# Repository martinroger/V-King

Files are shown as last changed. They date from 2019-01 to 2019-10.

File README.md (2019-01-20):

The target is to create a cheap 500mmx500mmx500mm version !

Original Readme by Roy :

# V-King Pro 3d Printer
The non rod CoreXY V-Slot 3d Printer by Roy Berntsen

In this repository you will find the print files, source files and documentation for the V-King 3D printer. If you are missing a part or information of feel free to file an issue on github

I would appreciate if you buy me a coffe to keep the pace going in this project:

<a href="https://www.buymeacoffee.com/pro3d" target="_blank">Buy Me A Coffee</a>

You can be a supporter of the develompent on patreon here: https://www.patreon.com/pro3d

Community links: https://www.facebook.com/vking3d/ - https://www.facebook.com/groups/viking3d/

Here is a video covering the basics and benefits of this design: https://youtu.be/wINF7qM0DQU

All files are released according to the following license unless specified differently in the file or directory:
CC-by-NC: http://creativecommons.org/licenses/by-nc/3.0/

Roy Berntsen - Research and Development

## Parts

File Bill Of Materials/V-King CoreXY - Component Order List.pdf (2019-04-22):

V-King - Components to Buy

ALL HARDWARE KIT HERE ->> | MakerSupplies V-King Mechanical Kit (http://makersupplies.dk/72-v-king-corexy-3d-printer)
Click link to product supplier | Research, Development & Design by: | Roy Berntsen
Part Name | Description | BOM Quantity Unit Price | | Bulk Price
Frame Parts | Complete Kit (http://makersupplies.dk/72-v-king-corexy-3d-printer)
2020 V-Slot 500 (http://[s0l0];/#/56-color-silver_grey_anodized/40-length-500mm) | OpenBuild V-Slot 500mm | 16 | EUR 5,0 | EUR 80,0
2020 V-Slot 480 (http://[s0l1];/#/56-color-silver_grey_anodized/40-length-500mm) | OpenBuild V-Slot 480mm (http://makersupplies.dk/linear-rail/188-linear-rail-custom-cut-v-slot-rail-per-cut.html) | 1 | EUR 6,0 | EUR 6,0
3 Way V-Slot Corner (http://makersupplies.dk/brackets/32-brackets-cube-corner-connector.html?search_query=3+way&results=18) | 3 Way Corner Bracket | 8 | EUR 4,0 | EUR 32,0
2028 Corner Bracket (http://s.click.aliexpress.com/e/BqJqfQF) | Frame Corner Joint Brackets | 20 | | 7,00
Wheels
Solid V-Wheel Kit (http://makersupplies.dk/wheels/67-wheels-solid-v-wheel-kit.html) | OpenBuild V-Slot Big Wheels | 21 | EUR 5,0 EUR 105,0
Estimated Frame Kit Price | | | | EUR 230,0
Component Part Name | BOM Quantity Bulk Quantity | Bulk Price
Build Plate 1400 cm^2 (http://clever3d.de/epages/7a4290fc-7c7f-46cc-9b99-eadef22228e2.sf/en_US/) | 360x410x8mm Aluminum | 1 | 1 | 90,00
Controller - MKS Gen L V1.0 (http://s.click.aliexpress.com/e/uB2fyVN) | Ramps Controller | 1 | 1 | 20,00
Controller LCD 12864 (http://s.click.aliexpress.com/e/bRJkG02c) | LCD Controller Panel | 1 | 1 | 12,00
Drivers - A4988 (http://s.click.aliexpress.com/e/cln5G0dw) | ZE Stepper Drivers | 2 | 4 | 10,00
Drivers - TMC2208 (http://s.click.aliexpress.com/e/bPs1Gu4g) | XY Stepper Drivers | 2 | 4 | 25,00
End Stop - Optical Sensor (http://s.click.aliexpress.com/e/Im2VNR3) | Optical Endstop Sensor | 2 | 6 | 3,00
Extruder (http://s.click.aliexpress.com/e/bH9je2h6) | Titan Original Here (https://e3d-online.com/titan-extruder) | 1 | 1 | 20,00
Fan - Layer Fan 12/24V (http://s.click.aliexpress.com/e/EDFqKMu) | Fan for filament cooling | 1 | 1 | 5,00
GT2 Idler Pulley 20T (http://s.click.aliexpress.com/e/bNQNlORm) | Thoothed Idler Pulley | 8 | 10 | 10,00
GT2 Idler Pulley Smooth (http://s.click.aliexpress.com/e/bNQNlORm) | Smooth Pulley | 10 | 10 | 10,00
GT2 Motor Pulley 20T (http://s.click.aliexpress.com/e/b71XZzSu) | Thoothed Motor Pulley | 4 | 4 | 5,00
GT2 Timing Belt (http://s.click.aliexpress.com/e/E6yV3BM) | Reinforced Timing Belt | 7 | 10 | 10,00
Hotend - J-Head/E3d Clone (https://www.aliexpress.com/store/product/3D-printer-parts-e3d-V6-24V-remote-Bowen-print-J-head-Hotend-extruder-1meter-Teflon-tube/1494743_32869495725.html) | e3d V6 Original Here (https://e3d-online.com/v6) | 1 | 1 | 5,00
Power Supply 24V (http://s.click.aliexpress.com/e/bUwbSgN2) | 240W 24V PSU | 1 | 1 | 20,00
Power Switch - Fused (http://s.click.aliexpress.com/e/b2QUtcoC) | AC Inlet to PSU with Fuse | 1 | 1 | 7,00
Probe - 3D Touch (http://s.click.aliexpress.com/e/bhxMAOUo) | Original Probe here (https://www.antclabs.com/) | 1 | 1 | 15,00
Silicone Heatpad 350*400 (http://s.click.aliexpress.com/e/bWGHdGPI) | Ask for 110 AC if needed | 1 | 1 | 30,00
Solid State Relay (http://s.click.aliexpress.com/e/iQVbe2z) | SSR 40A | 1 | 1 | 4,00
Stepper Motor 1.7A Nema 17 (http://s.click.aliexpress.com/e/dZN2aDi) | Nema 17 Stepper motor | 4 | 4 | 30,00
Worm Gear (https://rover.ebay.com/rover/1/711-53200-19255-0/1?icep_id=114&ipn=icep&toolid=20004&campid=5338443015) | 1:20 Worm Gear Set | 1 | 1 | 10,00
Worm Gear Bearings (http://s.click.aliexpress.com/e/c5afxP5q) | 5id-16od-5w Ball bearings | 4 | 10 | 4,00
Worm Gear Rod (https://rover.ebay.com/rover/1/711-53200-19255-0/1?icep_id=114&ipn=icep&toolid=20004&campid=5338443015) | 5mm X 555 mm Steel rod | 1 | 1 | 20,00
Estimated Component Retail Price | No fasteners or cables included | EUR 365,0
Komplete Mechanichal Kit | Fasteners included | | | Bulk Price
MakerSupplies Mechanical Kit (http://makersupplies.dk/72-v-king-corexy-3d-printer) | | | | EUR 315,00

If you like to support - Buy me a coffe here: https://www.buymeacoffee.com/pro3d

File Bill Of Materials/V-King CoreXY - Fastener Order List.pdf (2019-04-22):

List of Fasteners to buy at any hardware supplier

Research, Development & Design by

## Roy Berntsen

Fasteners | Type | Order Quantity Est. Unit Price Est. Bulk Price
M3 NUT | Hex Nut - M3 | 25 | 0,1 | 2,5
M3 WASHER | Washer Simple M3 | 25 | 0,1 | 2,5
M3x10 | DIN 912 | 25 | 0,1 | 2,5
M3X25 | DIN 912 | 10 | 0,1 | 1
M3x8 | DIN 912 | 25 | 0,1 | 2,5
M4 Hex NUT | Hex Nut - M4 | 10 | 0,1 | 1
M4 Hex Nut lock | Hex Locking Nut - M4 | 10 | 0,1 | 1
M4 WASHER | Washer Simple M4 | 10 | 0,1 | 1
M4x16 | DIN 912 | 10 | 0,1 | 1
M4x20 | DIN 912 | 10 | 0,1 | 1
M5 GT2 Idler Shim | Precision Shim for GT2 idlers/pulleys | 25 | 0,1 | 2,5
M5 Hex Nut | Standard Nut M5 | 20 | 0,1 | 2
M5 Hex Nut lock | Hex Locking Nut - m5 | 40 | 0,1 | 4
M5 T-Nut Hammer (http://s.click.aliexpress.com/e/bswuOzVQ) | Drop In type Hammer Nut | 50 | 0,1 | 5
M5 T-Nut Square (http://s.click.aliexpress.com/e/bn7WcvoG) | T-Nut Sqare M5 | 100 | 0,1 | 10
M5 WASHER | Washer Simple M5 | 150 | 0,1 | 15
M5x10 | DIN 912 | 100 | 0,1 | 10
M5x14 | DIN 912 | 10 | 0,1 | 1
M5x20 Hex | Hex Head | 20 | 0,1 | 2
M5X25 | DIN 912 | 10 | 0,1 | 1
M5x30 | DIN 912 | 20 | 0,1 | 2
M5x35 | DIN 912 | 10 | 0,1 | 1
M5x35 HEX | Hex Head | 10 | 0,1 | 1
M5x8 Countersink (http://s.click.aliexpress.com/e/cBsxDBlm) | DIN 7991 | 25 | 0,1 | 2,5
Estimated fastener price in total: | 75
Cables | Type | Order Quantity Est. Unit Price Est. Bulk Price

If you like to support - Buy me a coffe here: https://www.buymeacoffee.com/pro3d

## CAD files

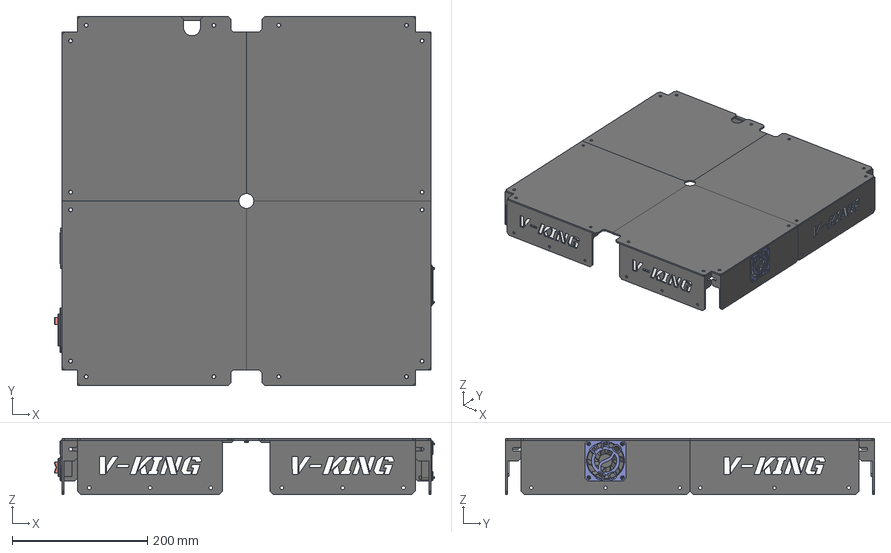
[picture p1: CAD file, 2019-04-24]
Source Files/STEP Files/Bottom Cabinet Assy v4.step
562.7 x 546.0 x 83.0 mm
V-King Led Plate x 6
Fan Grill 60 x 2
Fan House
Fan
M3 WASHER x 4
M3 NUT x 4
M3x20 x 4
Enclosure Lid AD x 2
Enclosure Lid BC
Enclosure Lid B

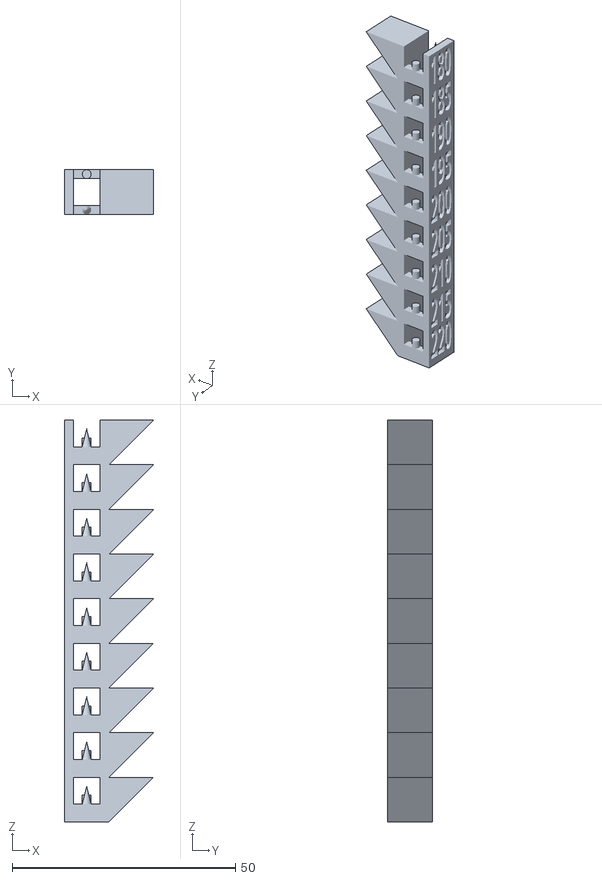
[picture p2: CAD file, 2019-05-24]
Part Print Files/Calibration Files/Temp Tower.stl
20.0 x 10.0 x 90.0

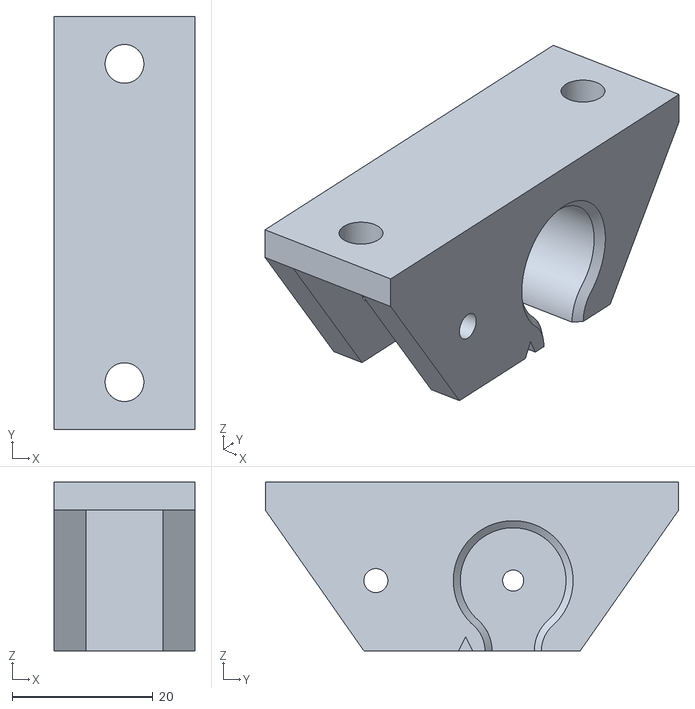
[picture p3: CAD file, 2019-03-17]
Part Print Files/Optional Files/3mm Idler Brackets/Z Idler_3mm Top Mount_R_1x.stl
20.0 x 58.7 x 24.0

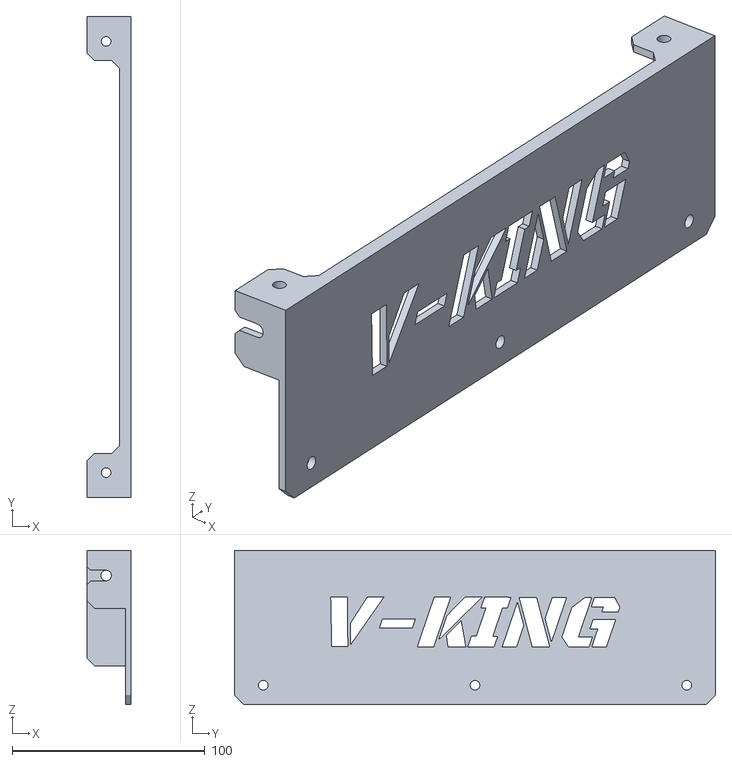
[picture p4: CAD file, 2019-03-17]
Part Print Files/Optional Files/Bottom Enclosure Files/Cover Side B2.stl
23.0 x 250.0 x 80.0

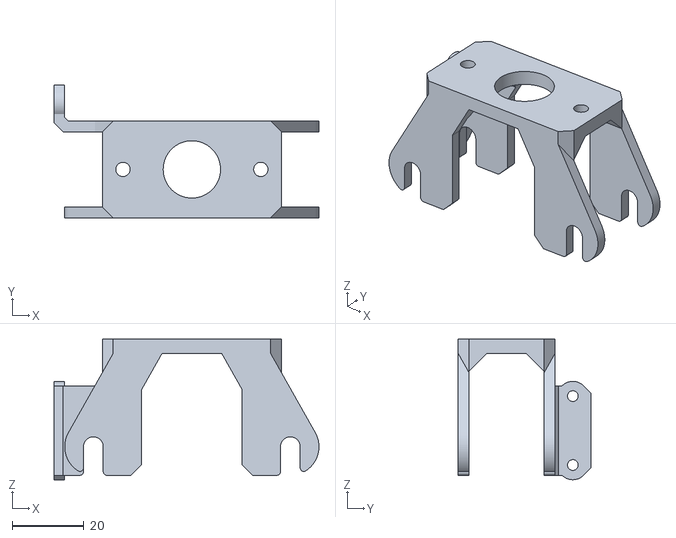
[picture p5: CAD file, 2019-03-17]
Part Print Files/Optional Files/Bowden Support/Bowden Carrier Buddy Support.stl
74.0 x 37.0 x 39.2

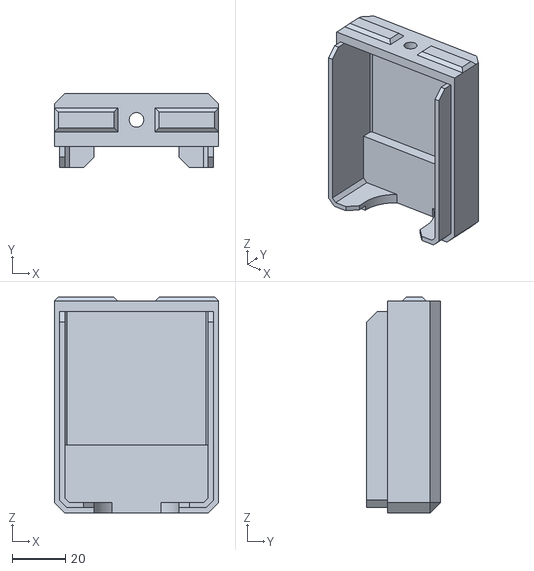
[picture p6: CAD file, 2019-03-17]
Part Print Files/Optional Files/Junction Box/Junction Base.stl
62.0 x 28.0 x 81.5

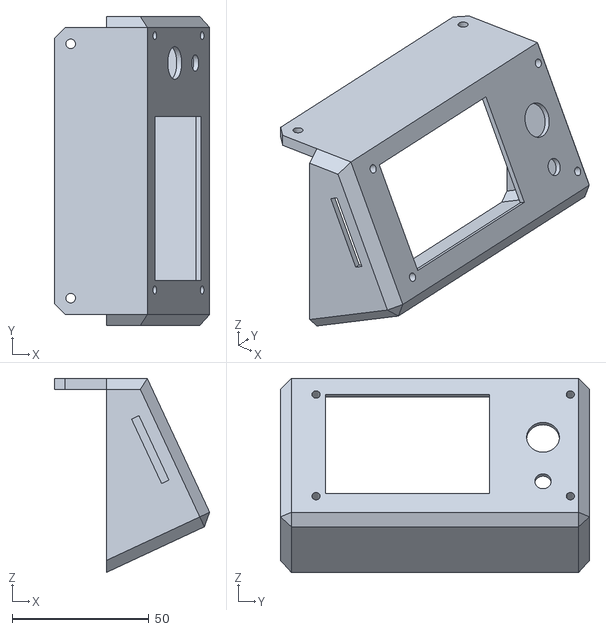
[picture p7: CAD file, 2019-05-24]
Part Print Files/Optional Files/Mini12864 LCD Cabinet.stl
56.8 x 113.0 x 71.0

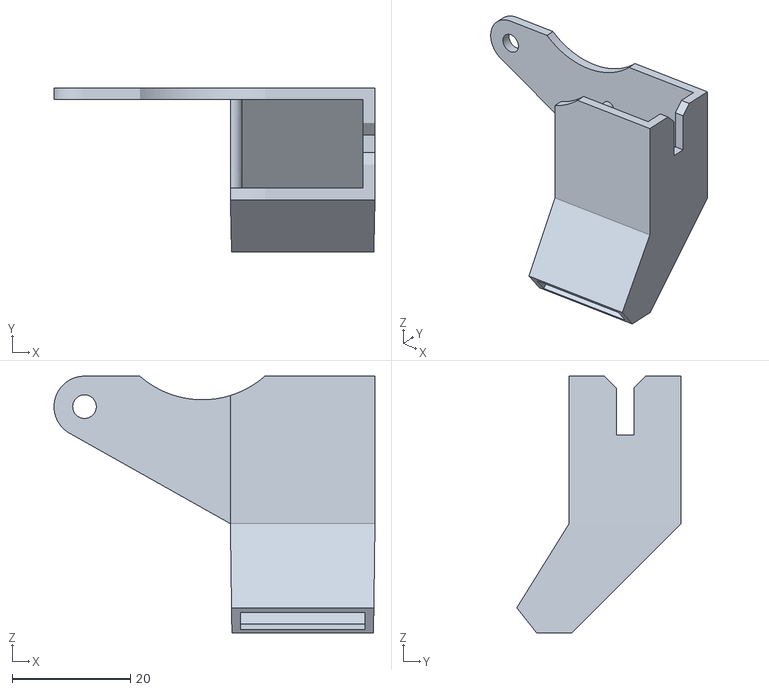
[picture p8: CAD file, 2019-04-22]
Part Print Files/Optional Files/Misc/5015 Layer Fan - Side Blower_1x.stl
54.4 x 27.9 x 43.5

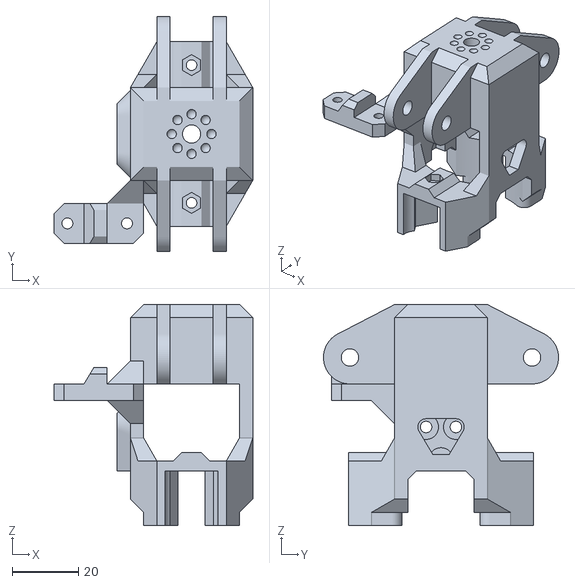
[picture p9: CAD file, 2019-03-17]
Part Print Files/Optional Files/X-Carriers/X-Carrier Chimera.stl
60.0 x 71.0 x 66.8

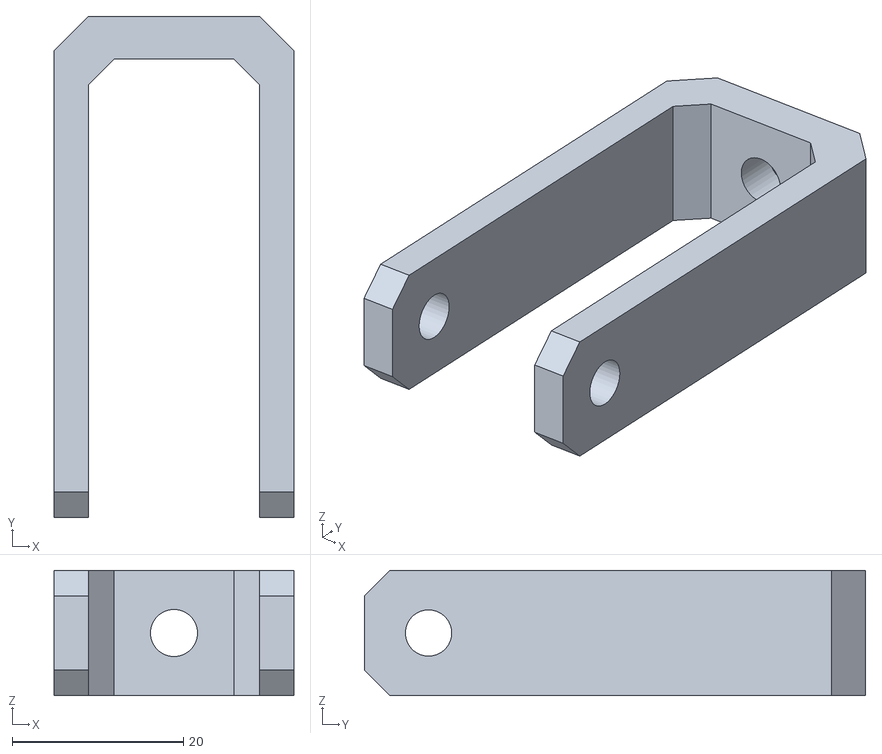
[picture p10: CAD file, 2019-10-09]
Part Print Files/Stock Part Files/Base Frame Parts/XY Belt Tensioner/XY Belt Tension Fork_2x_SN_BO.stl
28.0 x 58.5 x 14.6

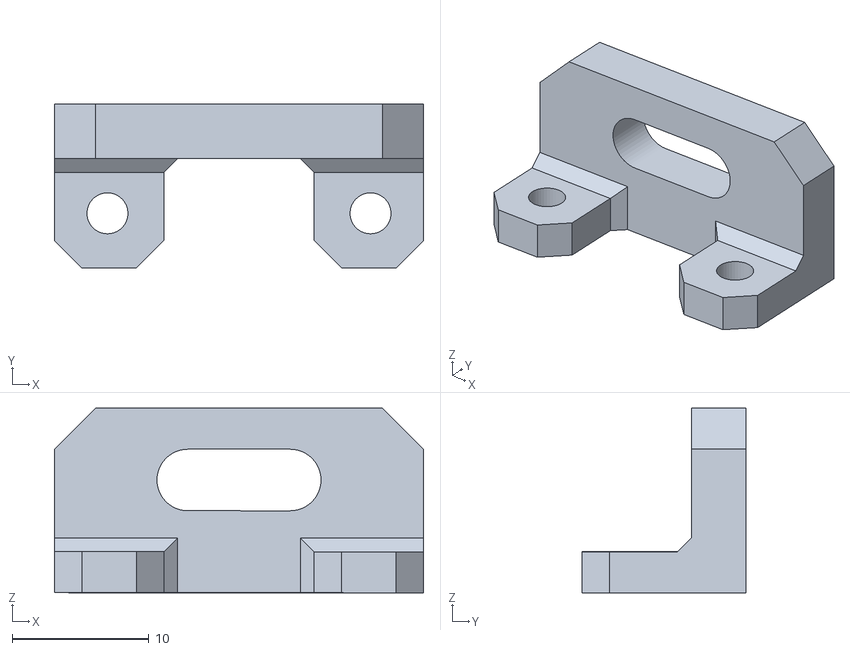
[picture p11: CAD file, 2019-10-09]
Part Print Files/Stock Part Files/Base Frame Parts/Y EndStop Bracket_1x_SN_BO.stl
27.0 x 12.0 x 13.5

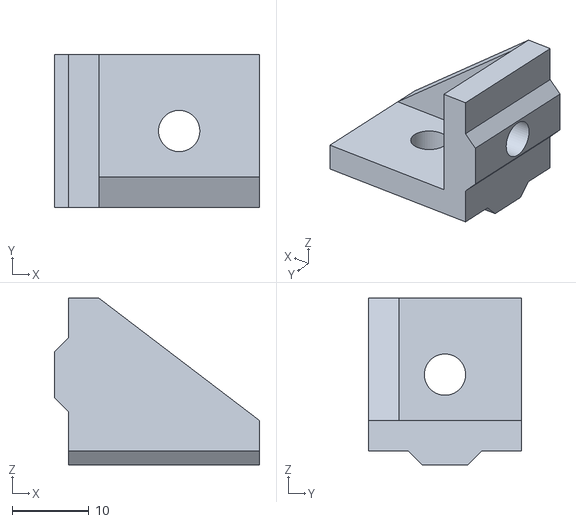
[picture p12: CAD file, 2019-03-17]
Part Print Files/Stock Part Files/Bed Supports/Bed L Bracket_4x.stl
26.8 x 20.0 x 21.8

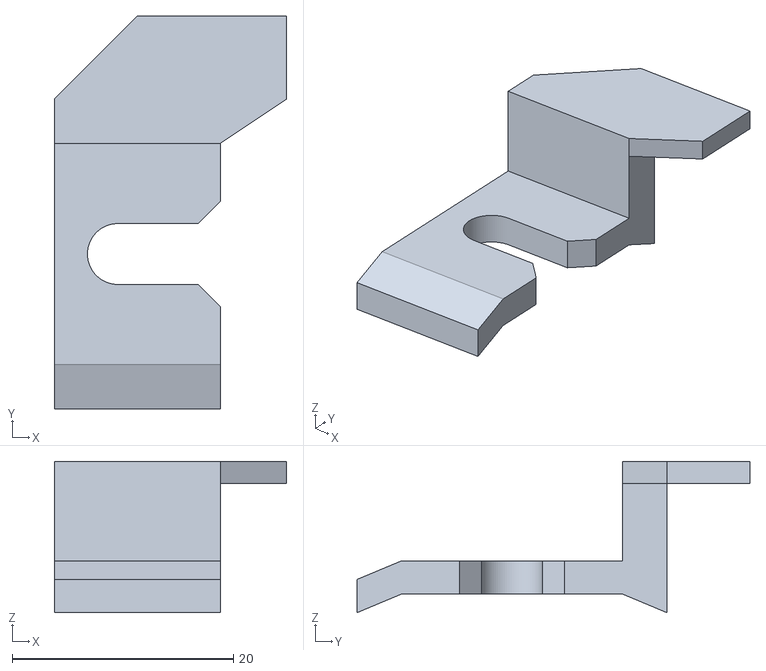
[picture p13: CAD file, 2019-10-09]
Part Print Files/Stock Part Files/X Axis Parts/X Carrier Parts/X EndStop Flag_1x.stl
21.0 x 35.5 x 13.7

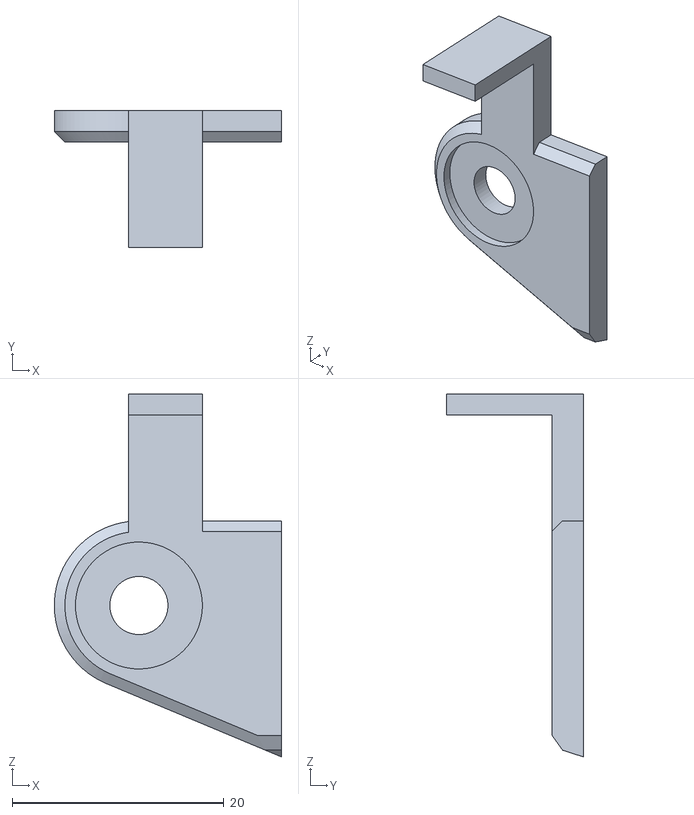
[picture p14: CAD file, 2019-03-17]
Part Print Files/Stock Part Files/X Axis Parts/Y EndStop Flag_1x.stl
21.5 x 13.0 x 34.3

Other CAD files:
Part Print Files/Stock Part Files/Z Drive Parts/Z Belt Anchor Lid R_1x.stl
Part Print Files/Tools/Bed Frame Hooks.stl
Part Print Files/Tools/Test Jig Files/e3d Fan Buddy.stl
Source Files/STEP Files/bullshit.step
Part Print Files/Calibration Files/Stringing_Test.stl
Part Print Files/Optional Files/3mm Idler Brackets/XY Idler_3mm Corner_2x.stl
Part Print Files/Optional Files/3mm Idler Brackets/Z Idler_3mm Bed Bracket_2x.stl
Part Print Files/Optional Files/3mm Idler Brackets/Z Idler_3mm Bed Support_2x.stl
Part Print Files/Optional Files/3mm Idler Brackets/Z Idler_3mm Top Mount_M_1x.stl
Part Print Files/Optional Files/Bottom Enclosure Files/2020 Cable Sleeve Buddy.stl
Part Print Files/Optional Files/Bottom Enclosure Files/Center Lid Nut.stl
Part Print Files/Optional Files/Bottom Enclosure Files/Center Lid Support.stl
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

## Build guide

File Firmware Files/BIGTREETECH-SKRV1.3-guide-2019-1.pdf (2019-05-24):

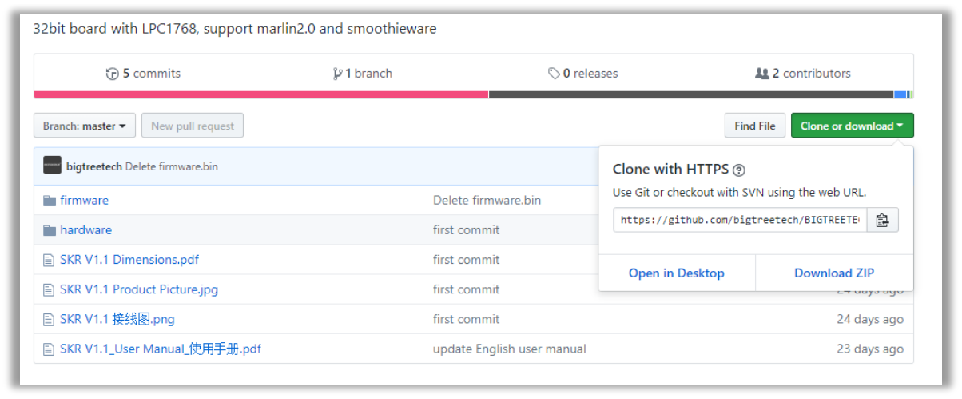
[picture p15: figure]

BIGTREETECH SKR V1.3 guide 2019 – V1 by Jupa Creations Page 1

BIGTREETECH/BIQU SKR V1.3 instruction guide by Jupa Creations

All official information like schematics and hardware about this 32 bits 3D printer mainboard can be found on the BIGTREETECH official GITHUB site. (https://github.com/bigtreetech/BIGTREETECH-SKR-V1.3)

This instruction guide is to show you how to install Marlin 2.0 firmware to the SKR V1.3 board in general. It does not take in account machine and other hardware specific settings!

You can use VSCode or Atom.IO + Platform IO to compile Marlin2.0 to BIGTREETECH/BIQU SKR V1.3

Intended for use with a REPRAP_DISCOUNT_FULL_GRAPHIC_SMART_CONTROLLER 128x64 LCD display by standard with two 10 wire ribbon cables.

Download the Marlin2.0 firmware from Marlin 2.0 github firmware version (https://github.com/MarlinFirmware/Marlin/tree/bugfix-2.0.x) and click.

Click “Download ZIP”

Remark if you use Octoprint, do not use the BIGTREETECH firmware version itself but download Marlin 2.0 github firmware version (https://github.com/MarlinFirmware/Marlin/tree/bugfix-2.0.x) and modify it to your needs.

When the download is complete, unzip the file to a known place.

N this example we use VScode

Download the VScode from https://code.visualstudio.com/Download. Choose the version which is compliant with your PC operating system.

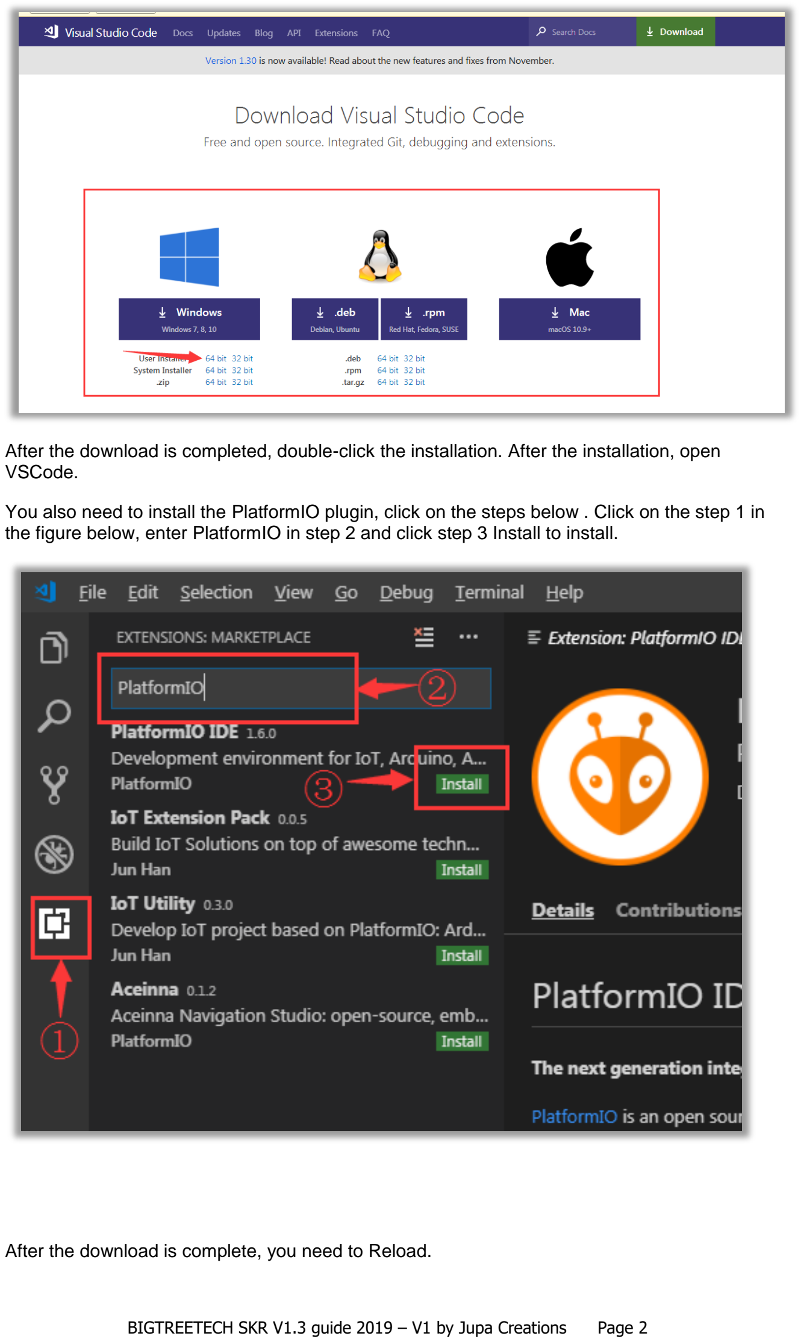
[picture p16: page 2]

BIGTREETECH SKR V1.3 guide 2019 – V1 by Jupa Creations Page 2

After the download is completed, double-click the installation. After the installation, open VSCode.

You also need to install the PlatformIO plugin, click on the steps below . Click on the step 1 in the figure below, enter PlatformIO in step 2 and click step 3 Install to install.

After the download is complete, you need to Reload.

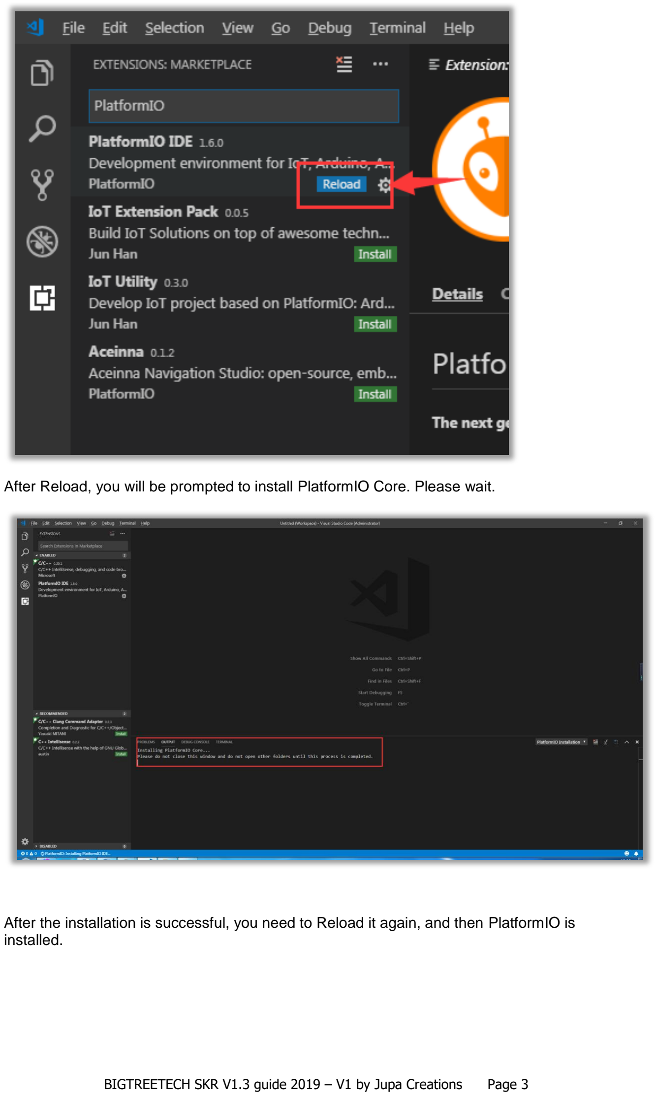
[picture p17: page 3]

BIGTREETECH SKR V1.3 guide 2019 – V1 by Jupa Creations Page 3

After Reload, you will be prompted to install PlatformIO Core. Please wait.

After the installation is successful, you need to Reload it again, and then PlatformIO is installed.

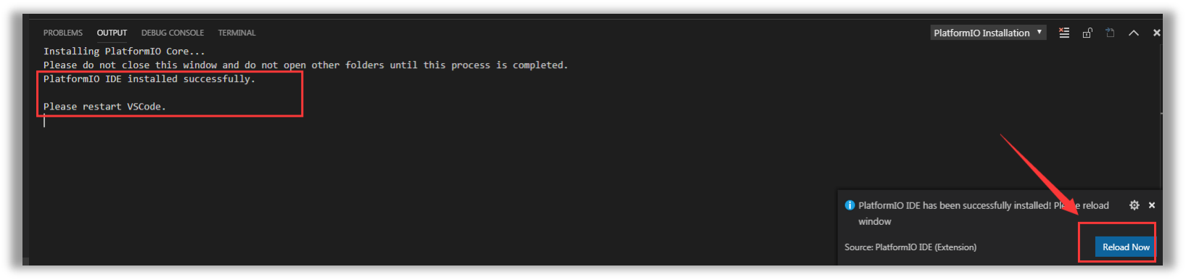
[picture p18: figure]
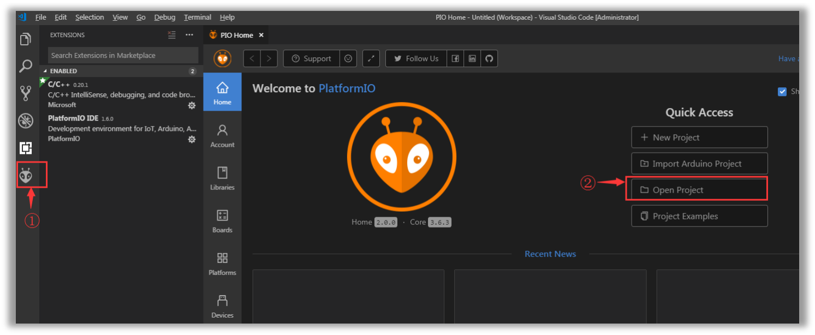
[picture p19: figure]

BIGTREETECH SKR V1.3 guide 2019 – V1 by Jupa Creations Page 4

In the lower left corner of VSCode, you can see the icon (1), which is PlatformIO plug-in. Click
(2) Open Project to Open the Project.

Find the marlin2.0 source directory where you extracted in the very first step, and click Open.

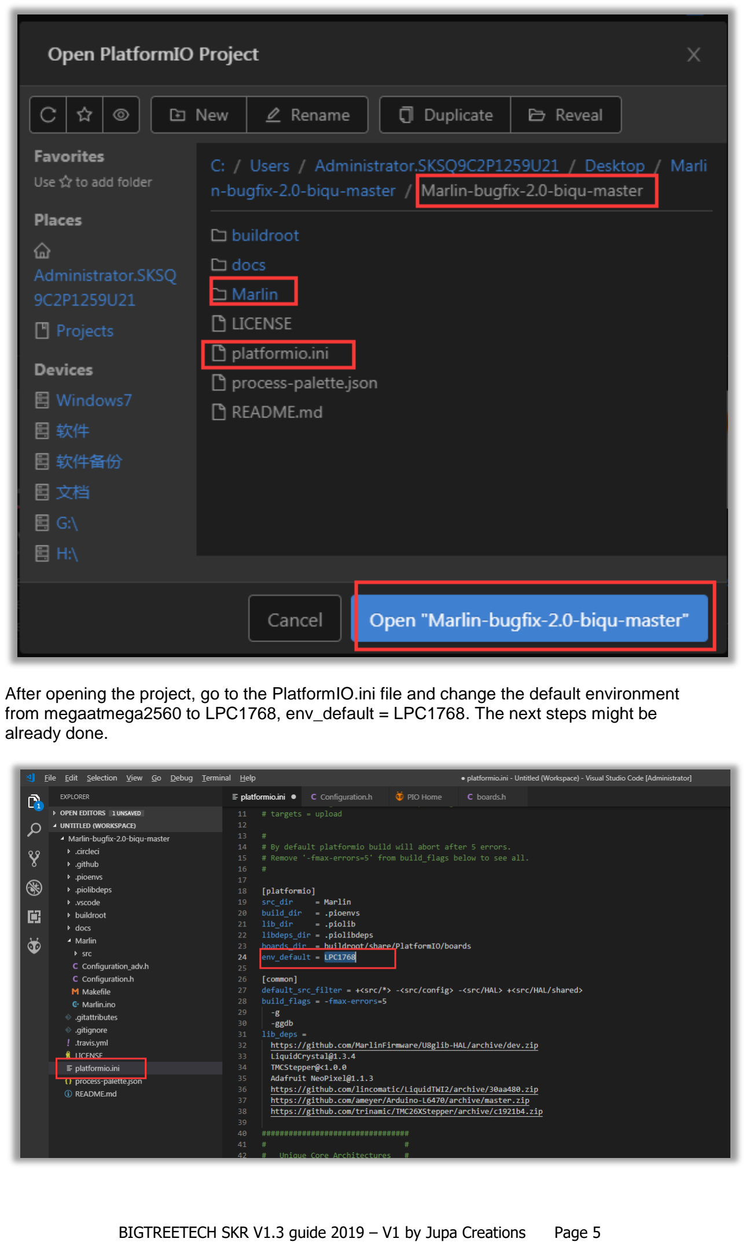
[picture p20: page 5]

BIGTREETECH SKR V1.3 guide 2019 – V1 by Jupa Creations Page 5

After opening the project, go to the PlatformIO.ini file and change the default environment from megaatmega2560 to LPC1768, env_default = LPC1768. The next steps might be already done.

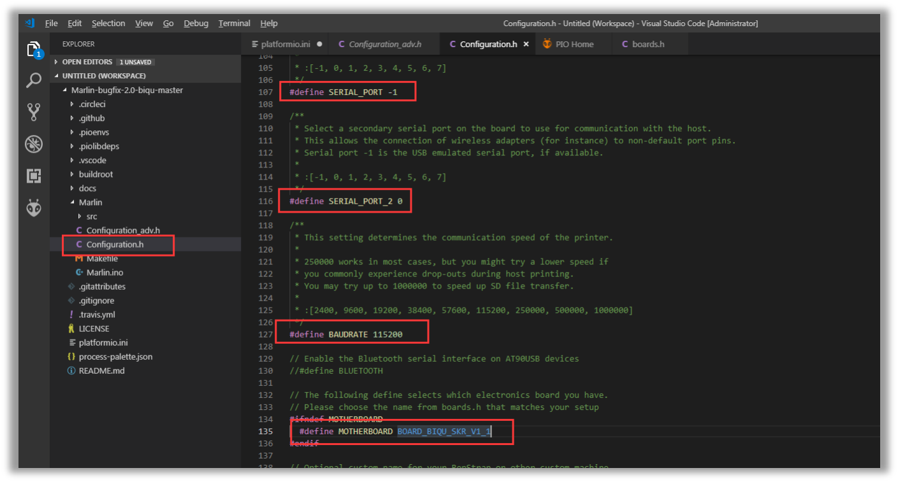
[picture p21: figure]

BIGTREETECH SKR V1.3 guide 2019 – V1 by Jupa Creations Page 6

Then go to the configuration.h file and if not yet done modify it to

#define SERIAL_PORT 0

#define SERIAL_PORT_2 -1

#define BAUDRATE 115200

#define MOTHERBOARD BOARD_BIQU_SKR_V1_3

If you like to use a BL-touch you have to change some code.

In the same Configuration.h

Modify the following lines:

//#define BLTOUCH and change to
#define BLTOUCH

//#define AUTO_BED_LEVELING_BILINEAR and change to #define AUTO_BED_LEVELING_BILINEAR

// #define Z_SAFE_HOMING and change to
#define Z_SAFE_HOMING

// #define ENCODER_PULSES_PER_STEP 4 and change to #define ENCODER_PULSES_PER_STEP 4

// #define REVERSE_ENCODER_DIRECTION and change to
#define REVERSE_ENCODER_DIRECTION

//#define REPRAP_DISCOUNT_FULL_GRAPHIC_SMART_CONTROLLER and change to #define REPRAP_DISCOUNT_FULL_GRAPHIC_SMART_CONTROLLER

If you like to activate Babystepping switch to Configuration_adv.h

//#define BABYSTEPPING and change to
#define BABYSTEPPING

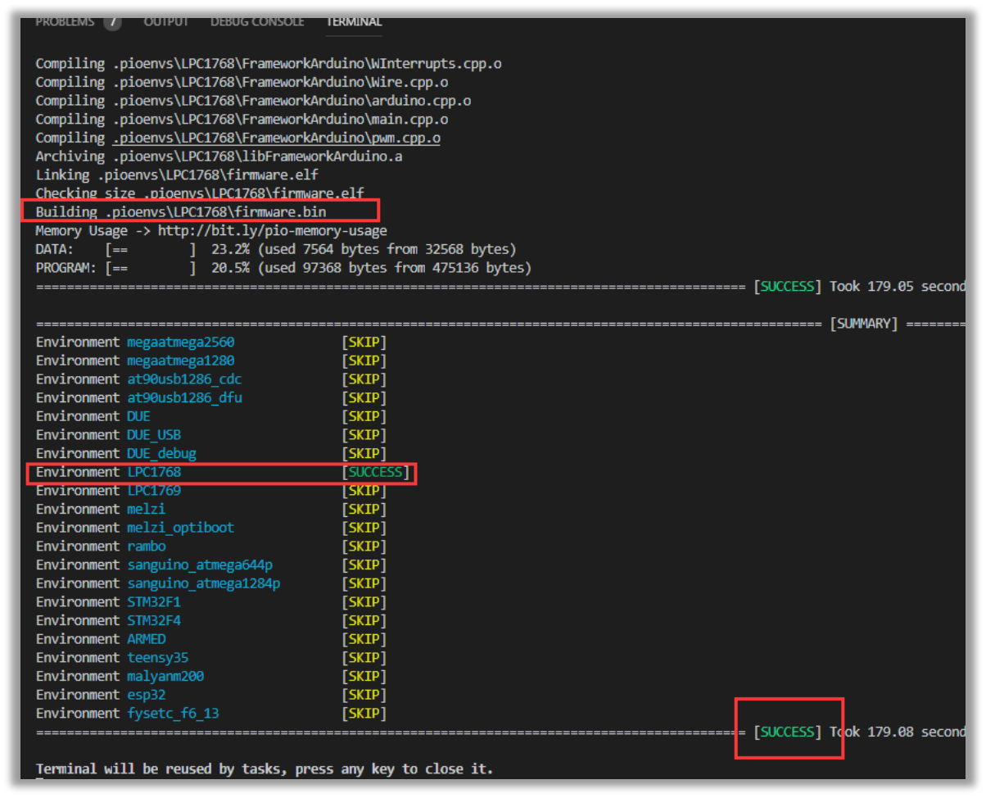
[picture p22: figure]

BIGTREETECH SKR V1.3 guide 2019 – V1 by Jupa Creations Page 7

//#define DOUBLECLICK_FOR_Z_BABYSTEPPING and change to #define DOUBLECLICK_FOR_Z_BABYSTEPPING

//#define BABYSTEP_ZPROBE_OFFSET and change to #define BABYSTEP_ZPROBE_OFFSET

//#define BABYSTEP_ZPROBE_GFX_OVERLAY and change to #define BABYSTEP_ZPROBE_GFX_OVERLAY

#define BABYSTEP_MULTIPLICATOR 1 and change to

#define BABYSTEP_MULTIPLICATOR 20

If your original BL-touch, clone TL-touch or clone BT-touch is dropping the pin during printing switch to Marlin/scr/inc/conditionals_LCD.h and change the following code:

#define BLTOUCH_STOW 100 // was 90

#define BLTOUCH_SELFTEST 130 // was 120

After the modification is completed, for VScode press the Ctrl+Shift+B keys to start compiling. PlatformIO will automatically download the compile component and then compile.

Compiling can take up to 5 minutes, so be patient.

After the compiling is successful, a “firmware.bin” file will be generated in the \pioenvs\LPC1768 directory. Copy this file to the TF card of the motherboard and reset or powercycle the motherboard, so that the firmware is burned into the motherboard.

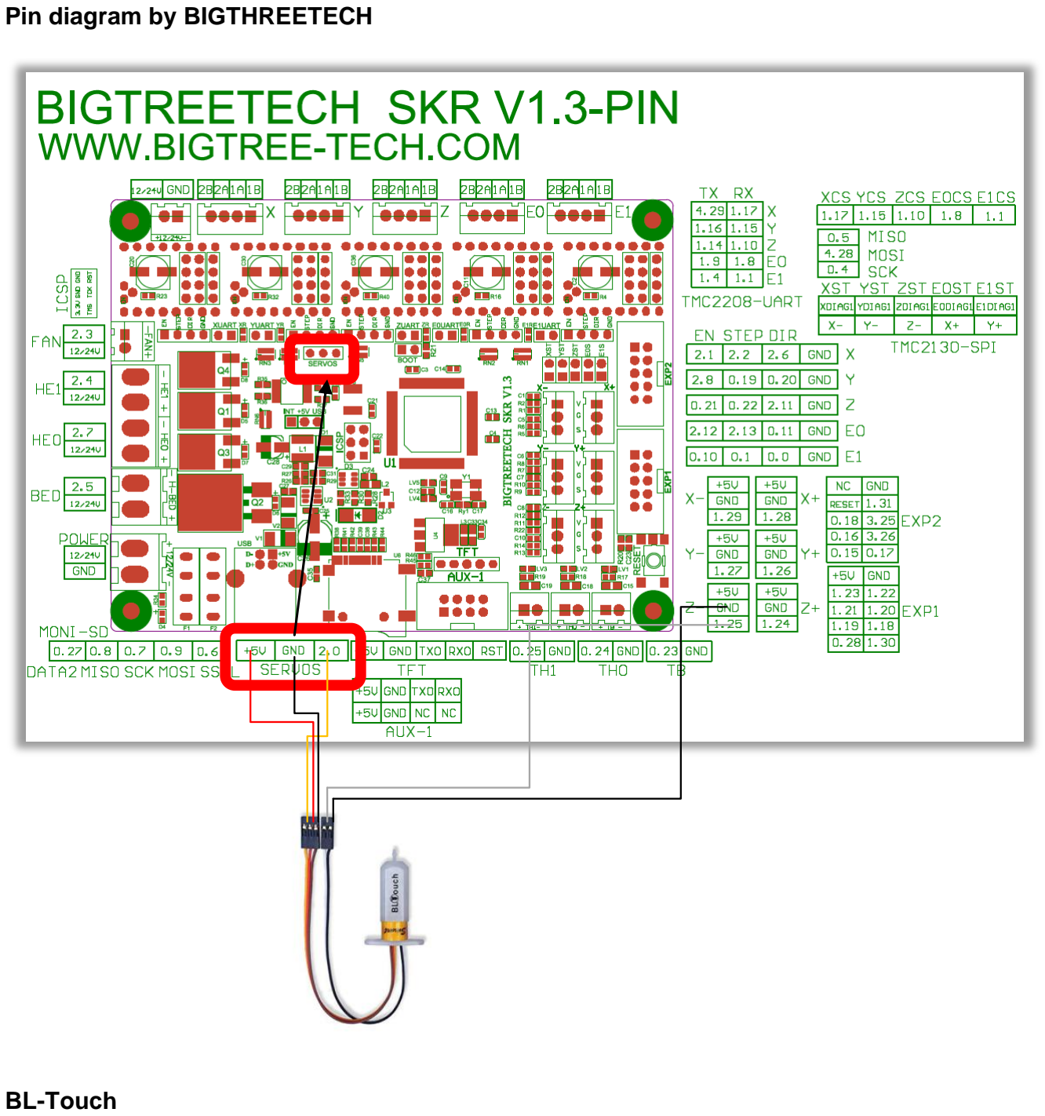
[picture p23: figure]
Pin diagram by BIGTHREETECH; BL-Touch

BIGTREETECH SKR V1.3 guide 2019 – V1 by Jupa Creations Page 8

The SKR V1.3 board has a dedicated Servo port.

Wire connections need to be checked before use!

For connecting the ANTCLABS BL-touch three wire cable to Servo port.
SKR V1.3 Board servo port = (+)(-)(puls) and BL-touch = (-)(+)(puls)
Positive (+) and Minus (-) need to be swapped in the BL-Touch connector or an intermediate connection cable need to be made. The two wire sensor cable connects to the (Z-) port.

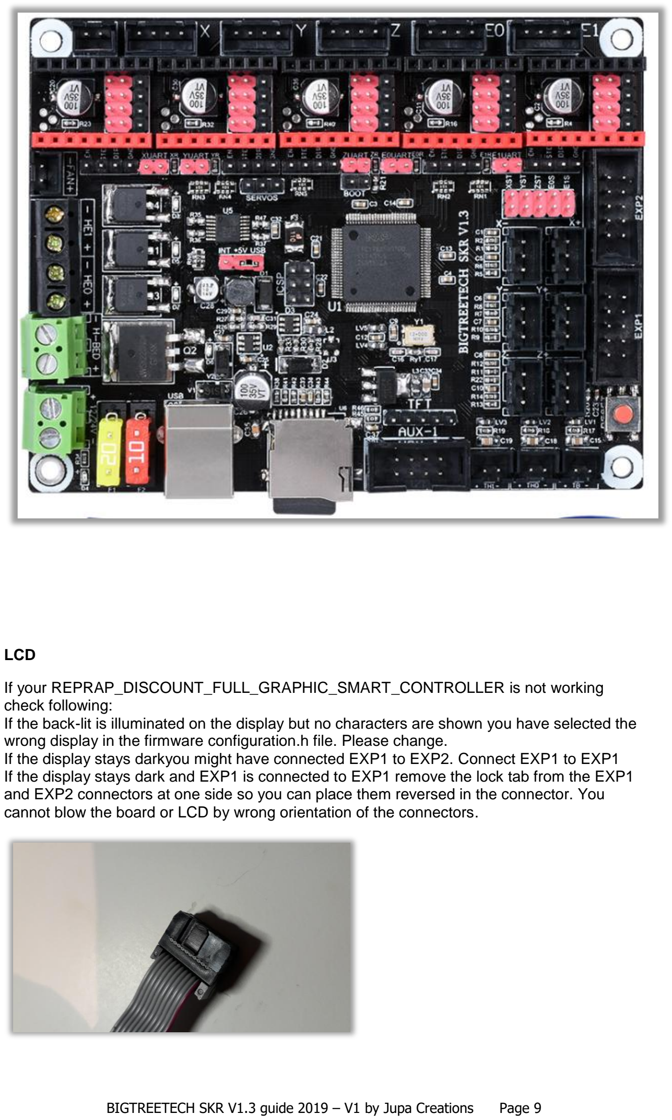
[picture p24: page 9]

BIGTREETECH SKR V1.3 guide 2019 – V1 by Jupa Creations Page 9

LCD

If your REPRAP_DISCOUNT_FULL_GRAPHIC_SMART_CONTROLLER is not working check following:
If the back-lit is illuminated on the display but no characters are shown you have selected the wrong display in the firmware configuration.h file. Please change.
If the display stays darkyou might have connected EXP1 to EXP2. Connect EXP1 to EXP1 If the display stays dark and EXP1 is connected to EXP1 remove the lock tab from the EXP1 and EXP2 connectors at one side so you can place them reversed in the connector. You cannot blow the board or LCD by wrong orientation of the connectors.

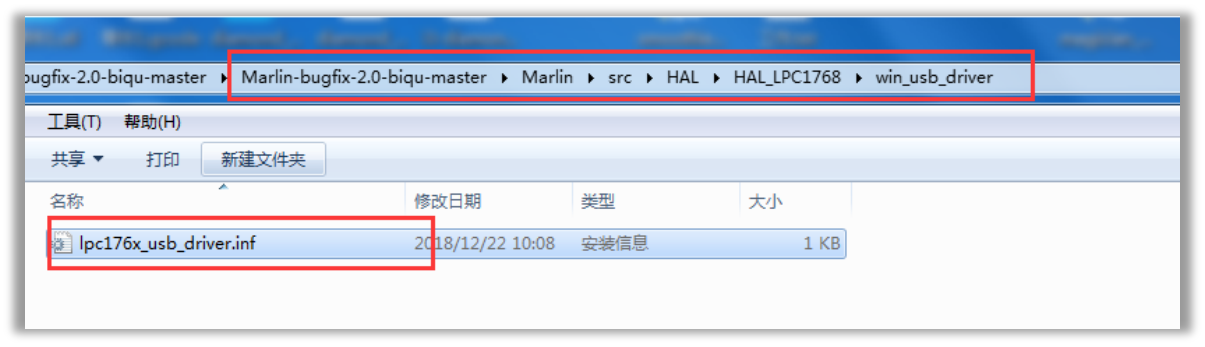
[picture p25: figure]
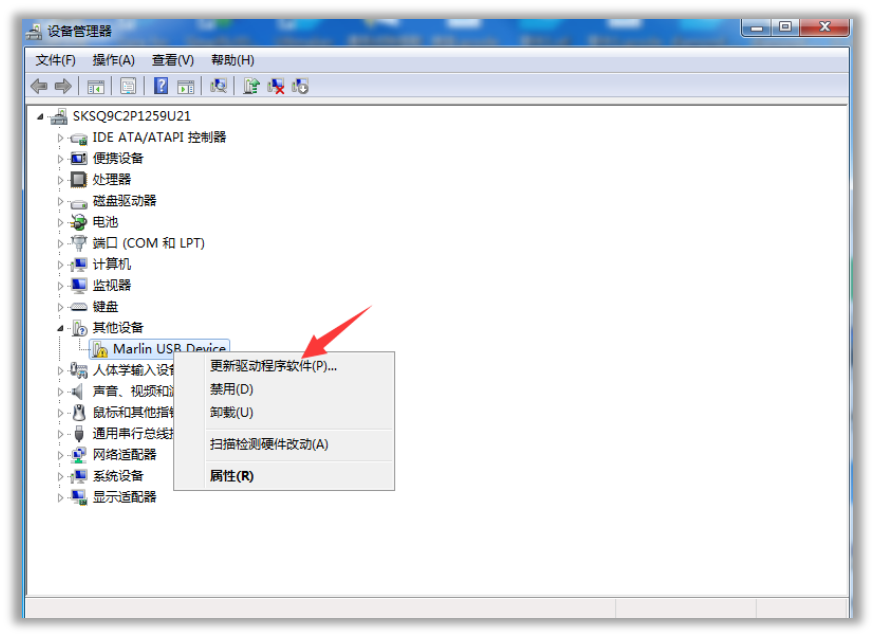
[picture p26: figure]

BIGTREETECH SKR V1.3 guide 2019 – V1 by Jupa Creations Page 10

In Windows 10 a driver called MARLIN will be automatically installed by plug & play when a USB cable is connected to the motherboard. It will show as a MARLIN port. Do not install any other USB driver or Smoothie drivers while usng Windows 10!

For other Windows operating systems the computer identification motherboard needs to install USB to serial port driver manually in the directory of the firmware as shown below. Because its path is too long, copy it to an easy to find location like to the desktop.

Open the Device manager, you can see that there is an unrecognized Marlin USB Device, click to update the driver software.

Browse the computer to find the driver software.

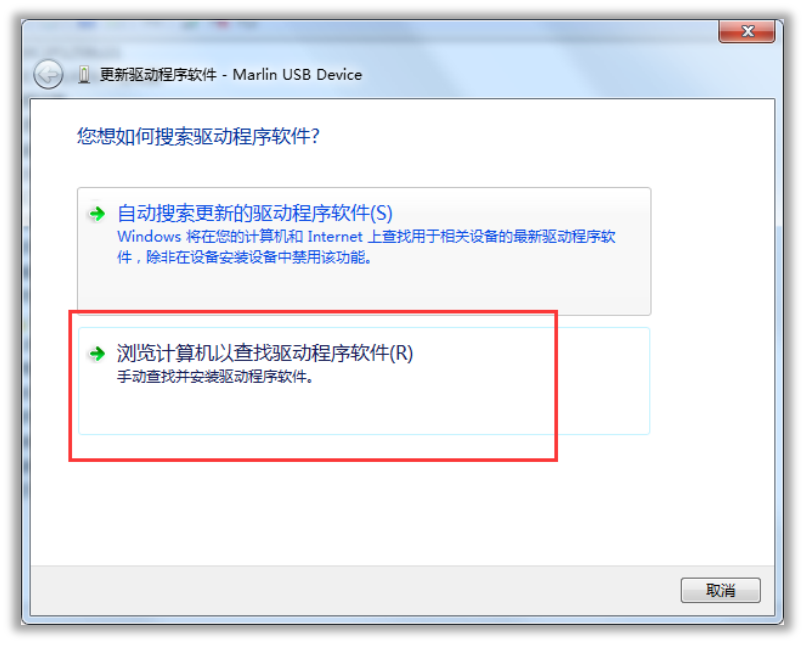
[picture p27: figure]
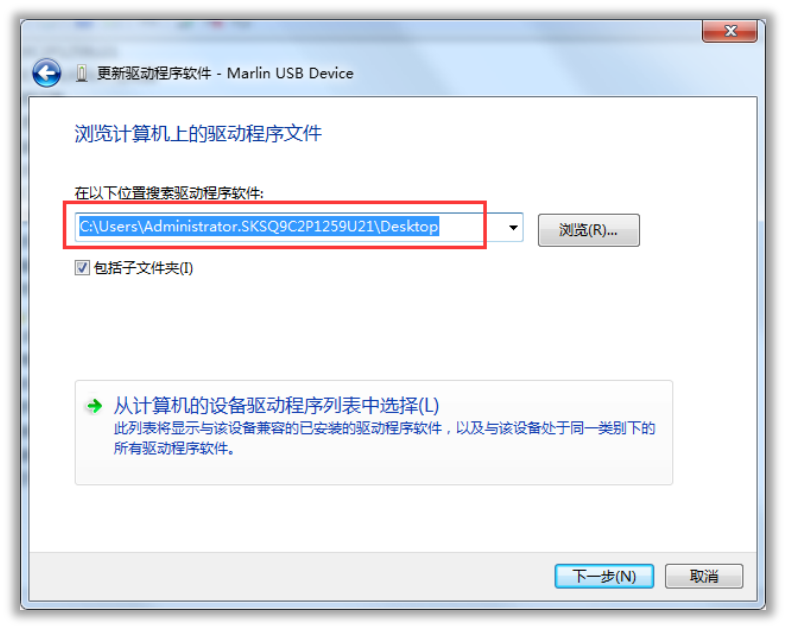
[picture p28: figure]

BIGTREETECH SKR V1.3 guide 2019 – V1 by Jupa Creations Page 11

Select the path as the directory where the lpc176x_usb_driver.inf driver is located. We copied it to the desktop before, so select the desktop location: C:\Users\(Users Name)\Desktop and click Next. Check with the below picture.

If you have firewall alerts, choose to always install this driver software.

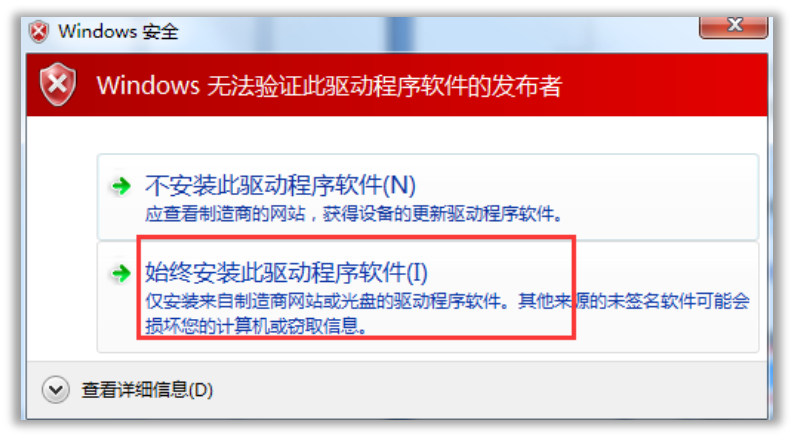
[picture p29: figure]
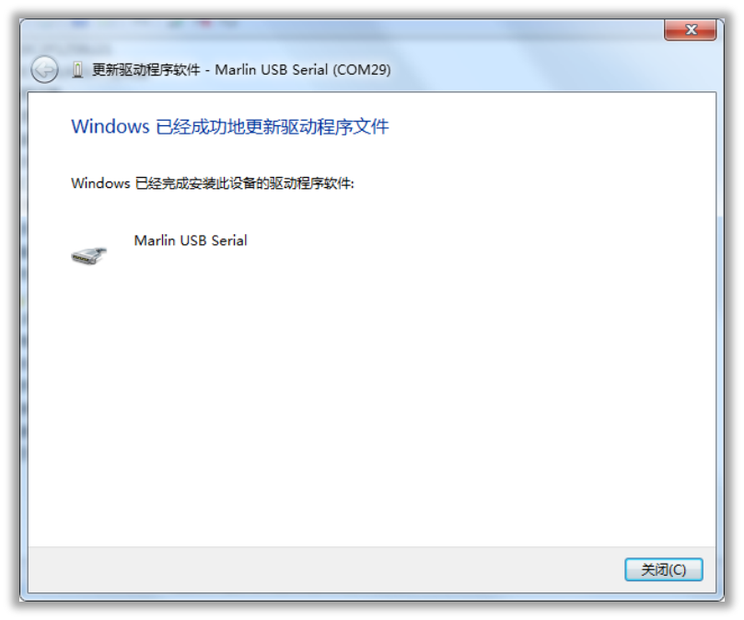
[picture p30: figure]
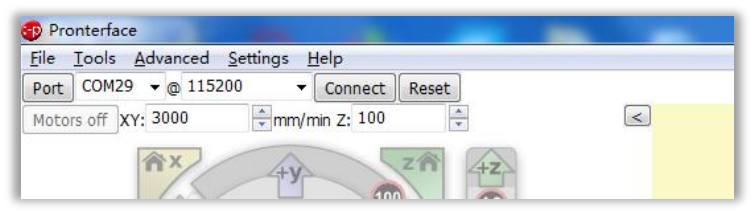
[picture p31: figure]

BIGTREETECH SKR V1.3 guide 2019 – V1 by Jupa Creations Page 12

If the install was successful, then the driver has been selected successfully. Remember the port number.

Open the Printrun/Pronterface online printing software as an example, select your com Port @115200, and then click Connect. Your COM port may be a different number.

On the right, you can see the printer is now online. This means that you have successfully connected to the printer. Now you can use your computer to control the printer

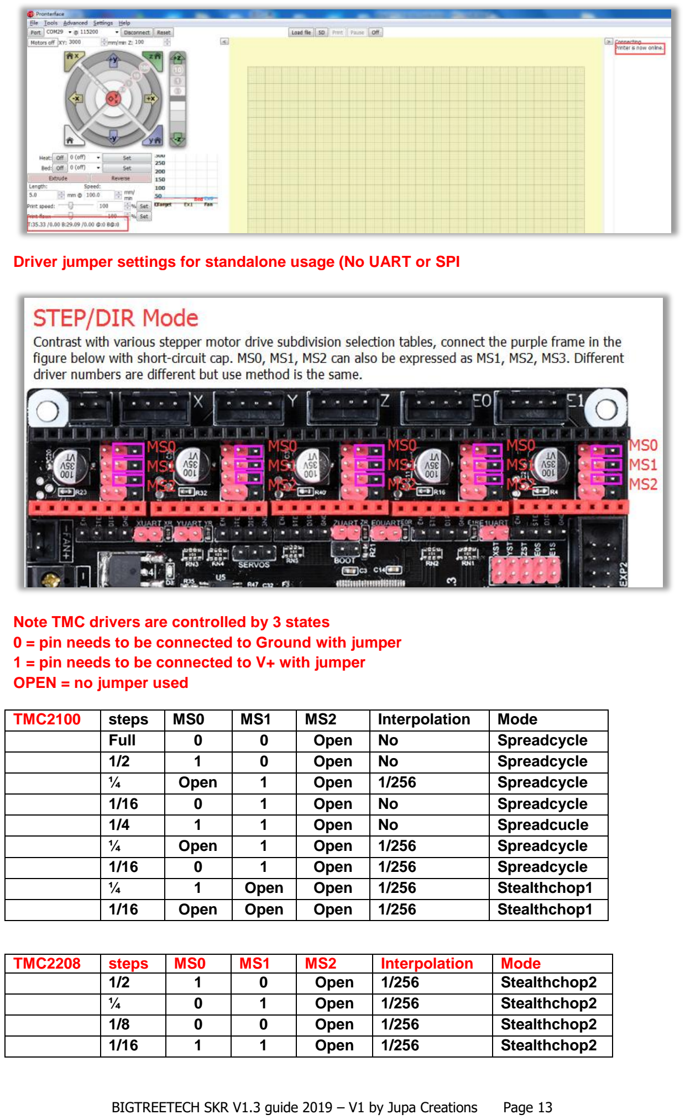
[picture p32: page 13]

BIGTREETECH SKR V1.3 guide 2019 – V1 by Jupa Creations Page 13

Driver jumper settings for standalone usage (No UART or SPI

Note TMC drivers are controlled by 3 states
0 = pin needs to be connected to Ground with jumper 1 = pin needs to be connected to V+ with jumper
OPEN = no jumper used
TMC2100 | steps | MS0 | MS1 | MS2 | Interpolation | Mode
| Full | 0 | 0 | Open | No | Spreadcycle
| 1/2 | 1 | 0 | Open | No | Spreadcycle
| ¼ | Open | 1 | Open | 1/256 | Spreadcycle
| 1/16 | 0 | 1 | Open | No | Spreadcycle
| 1/4 | 1 | 1 | Open | No | Spreadcucle
| ¼ | Open | 1 | Open | 1/256 | Spreadcycle
| 1/16 | 0 | 1 | Open | 1/256 | Spreadcycle
| ¼ | 1 | Open | Open | 1/256 | Stealthchop1
| 1/16 | Open | Open | Open | 1/256 | Stealthchop1
TMC2208 | steps | MS0 | MS1 | MS2 | Interpolation | Mode
| 1/2 | 1 | 0 | Open | 1/256 | Stealthchop2
| ¼ | 0 | 1 | Open | 1/256 | Stealthchop2
| 1/8 | 0 | 0 | Open | 1/256 | Stealthchop2
| 1/16 | 1 | 1 | Open | 1/256 | Stealthchop2

BIGTREETECH SKR V1.3 guide 2019 – V1 by Jupa Creations | Page 14
TMC2130 | steps | MS0 | MS1 | MS2 | Interpolation | Mode
| Full | 0 | 0 | Open | No | Spreadcycle
| ½ | 1 | 0 | Open | No | Spreadcycle
| ½ | Open | 1 | Open | 1/256 | Spreadcycle
| ¼ | 0 | 1 | Open | No | Spreadcycle
| 1/16 | 1 | 1 | Open | No | Spreadcycle
| ¼ | Open | 1 | Open | 1/256 | Spreadcycle
| 1/16 | 0 | Open | Open | 1/256 | Spreadcycle
| ¼ | 1 | Open | Open | 1/256 | Stealthchop1
| 1/16 | Open | Open | Open | 1/256 | Stealthchop1
A4988 | steps | MS0 | MS1 | MS2 | Interpolation | Mode
| Full | 0 | 0 | 0 | No | None
| ½ | 1 | 0 | 0 | No | None
| ¼ | 0 | 1 | 0 | No | None
| 1/8 | 0 | 1 | 0 | No | None
| 1/16 | 1 | 1 | 0 | No | None
DRV8825 | steps | MS0 | MS1 | MS2 | Interpolation | Mode
| Full | 0 | 0 | 0 | No | None
| ½ | 1 | 0 | 0 | No | None
| ¼ | 0 | 1 | 0 | No | None
| 1/8 | 1 | 1 | 0 | No | None
| 1/16 | 0 | 0 | 1 | No | None
| 1/32 | 1 | 1 | 1 | No | None
ST820 | steps | MS0 | MS1 | MS2 | Interpolation | Mode
| Full | 0 | 0 | 0 | No | None
| ½ | 0 | 0 | 1 | No | None
| ¼ | 1 | 0 | 0 | No | None
| 1/8 | 0 | 1 | 1 | No | None
| 1/16 | 1 | 0 | 0 | No | None
| 1/32 | 1 | 0 | 1 | No | None
| 1/128 | 1 | 1 | 0 | No | None
| 1/256 | 1 | 1 | 1 | No | None
LV8729 | Steps | MS0 | MS1 | MS2 | Interpolation | Mode
| Full | 0 | 0 | 0 | No | None
| ½ | 0 | 0 | 1 | No | None
| ¼ | 1 | 0 | 0 | No | None
| 1/8 | 0 | 1 | 1 | No | None
| 1/16 | 1 | 0 | 0 | No | None
| 1/32 | 1 | 0 | 1 | No | None
| 1/64 | 1 | 1 | 0 | No | None
| 1/128 | 1 | 1 | 1 | No | None

BIGTREETECH SKR V1.3 guide 2019 – V1 by Jupa Creations Page 15

Windows 10: Disable Signed Driver Enforcement

How can I install drivers that are not digitally signed?

Windows 10 enforces driver signatures by default. This can be disabled to install drivers that are not digitally signed. Use the following steps to disable driver signature enforcement.

1. Click the Start menu and select Settings.
2. Click Update and Security.
3. Click on Recovery.
4. Click Restart now under Advanced Startup.
5. Click Troubleshoot.
6. Click Advanced options.
7. Click Startup Settings.
8. Click on Restart.
9. On the Startup Settings screen press 7 or F7 to disable driver signature enforcement.

Your computer will restart and you will be able to install non-digitally signed drivers. If you restart your computer again the driver signature enforcement will be re-enabled.

If you are the creator of part of this document and you like your content to be removed please report.

This document is not created by BIGTREETECH!

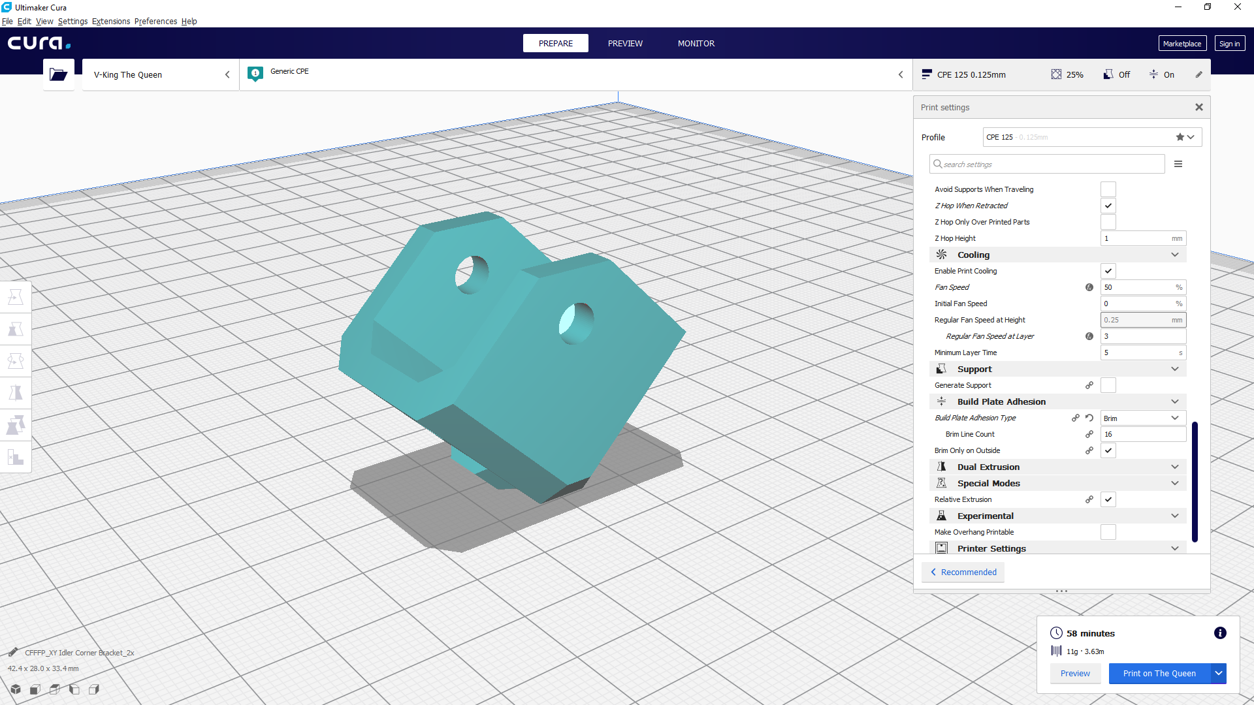
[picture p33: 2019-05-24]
Part Print Files/PrintHelp/Screenshots/XY Idler Corner Bracket_2x.png

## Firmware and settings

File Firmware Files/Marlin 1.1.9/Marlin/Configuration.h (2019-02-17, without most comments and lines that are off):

#define CONFIGURATION_H
#define CONFIGURATION_H_VERSION 010109
#define STRING_CONFIG_H_AUTHOR "(none, default config)" // Who made the changes.
#define SHOW_BOOTSCREEN
#define STRING_SPLASH_LINE1 SHORT_BUILD_VERSION // will be shown during bootup in line 1
#define STRING_SPLASH_LINE2 WEBSITE_URL         // will be shown during bootup in line 2
#define SERIAL_PORT 0
#define BAUDRATE 250000
  #define MOTHERBOARD BOARD_MKS_GEN_L
#define CUSTOM_MACHINE_NAME "V-KING CXY"
#define EXTRUDERS 1
#define DEFAULT_NOMINAL_FILAMENT_DIA 1.75
#define POWER_SUPPLY 0
#define TEMP_SENSOR_0 5
#define TEMP_SENSOR_1 0
#define TEMP_SENSOR_2 0
#define TEMP_SENSOR_3 0
#define TEMP_SENSOR_4 0
#define TEMP_SENSOR_BED 11
#define TEMP_SENSOR_CHAMBER 0
#define DUMMY_THERMISTOR_998_VALUE 25
#define DUMMY_THERMISTOR_999_VALUE 100
#define MAX_REDUNDANT_TEMP_SENSOR_DIFF 10
#define TEMP_RESIDENCY_TIME 10  // (seconds)
#define TEMP_HYSTERESIS 3       // (degC) range of +/- temperatures considered "close" to the target one
#define TEMP_WINDOW     1       // (degC) Window around target to start the residency timer x degC early.
#define TEMP_BED_RESIDENCY_TIME 10  // (seconds)
#define TEMP_BED_HYSTERESIS 3       // (degC) range of +/- temperatures considered "close" to the target one
#define TEMP_BED_WINDOW     1       // (degC) Window around target to start the residency timer x degC early.
#define HEATER_0_MINTEMP 5
#define HEATER_1_MINTEMP 5
#define HEATER_2_MINTEMP 5
#define HEATER_3_MINTEMP 5
#define HEATER_4_MINTEMP 5
#define BED_MINTEMP 5
#define HEATER_0_MAXTEMP 300
#define HEATER_1_MAXTEMP 300
#define HEATER_2_MAXTEMP 275
#define HEATER_3_MAXTEMP 275
#define HEATER_4_MAXTEMP 275
#define BED_MAXTEMP 150
#define PIDTEMP
#define BANG_MAX 255     // Limits current to nozzle while in bang-bang mode; 255=full current
#define PID_MAX BANG_MAX // Limits current to nozzle while PID is active (see PID_FUNCTIONAL_RANGE below); 255=full current
#define PID_K1 0.95      // Smoothing factor within any PID loop
  #define PID_AUTOTUNE_MENU // Add PID Autotune to the LCD "Temperature" menu to run M303 and apply the result.
  #define PID_FUNCTIONAL_RANGE 10 // If the temperature difference between the target temperature and the actual temperature
  #define  DEFAULT_Kp 15
  #define  DEFAULT_Ki 1.5
  #define  DEFAULT_Kd 50
#define PIDTEMPBED
#define MAX_BED_POWER 255 // limits duty cycle to bed; 255=full current
  #define  DEFAULT_bedKp 102
  #define  DEFAULT_bedKi 20
  #define  DEFAULT_bedKd 130
#define PREVENT_COLD_EXTRUSION
#define EXTRUDE_MINTEMP 170
#define PREVENT_LENGTHY_EXTRUDE
#define EXTRUDE_MAXLENGTH 500
#define THERMAL_PROTECTION_HOTENDS // Enable thermal protection for all extruders
#define THERMAL_PROTECTION_BED     // Enable thermal protection for the heated bed
#define COREXY
#define USE_XMIN_PLUG
#define USE_YMIN_PLUG
#define USE_ZMIN_PLUG
#define ENDSTOPPULLUPS
#define X_MIN_ENDSTOP_INVERTING false // set to true to invert the logic of the endstop.
#define Y_MIN_ENDSTOP_INVERTING false // set to true to invert the logic of the endstop.
#define Z_MIN_ENDSTOP_INVERTING false // set to true to invert the logic of the endstop.
#define X_MAX_ENDSTOP_INVERTING false // set to true to invert the logic of the endstop.
#define Y_MAX_ENDSTOP_INVERTING false // set to true to invert the logic of the endstop.
#define Z_MAX_ENDSTOP_INVERTING false // set to true to invert the logic of the endstop.
#define Z_MIN_PROBE_ENDSTOP_INVERTING false // set to true to invert the logic of the probe.
#define X_DRIVER_TYPE  TMC2208_STANDALONE
#define Y_DRIVER_TYPE  TMC2208_STANDALONE
#define Z_DRIVER_TYPE  DRV8825
#define E0_DRIVER_TYPE DRV8825
#define DEFAULT_AXIS_STEPS_PER_UNIT   { 80, 80, 3200, 406 }
#define DEFAULT_MAX_FEEDRATE          { 200, 200, 5, 100 }
#define DEFAULT_MAX_ACCELERATION      { 1500, 1500, 100, 10000 }
#define DEFAULT_ACCELERATION          1500    // X, Y, Z and E acceleration for printing moves
#define DEFAULT_RETRACT_ACCELERATION  3000    // E acceleration for retracts
#define DEFAULT_TRAVEL_ACCELERATION   1500    // X, Y, Z acceleration for travel (non printing) moves
#define DEFAULT_XJERK                 15.0
#define DEFAULT_YJERK                 15.0
#define DEFAULT_ZJERK                  0.3
#define DEFAULT_EJERK                 15.0
#define S_CURVE_ACCELERATION
#define Z_MIN_PROBE_USES_Z_MIN_ENDSTOP_PIN
#define BLTOUCH
#define X_PROBE_OFFSET_FROM_EXTRUDER 26  // X offset: -left  +right  [of the nozzle]
#define Y_PROBE_OFFSET_FROM_EXTRUDER 0  // Y offset: -front +behind [the nozzle]
#define Z_PROBE_OFFSET_FROM_EXTRUDER -1.1   // Z offset: -below +above  [the nozzle]
#define MIN_PROBE_EDGE 10
#define XY_PROBE_SPEED 6000
#define Z_PROBE_SPEED_FAST HOMING_FEEDRATE_Z
#define Z_PROBE_SPEED_SLOW (Z_PROBE_SPEED_FAST / 2)
#define Z_CLEARANCE_DEPLOY_PROBE   10 // Z Clearance for Deploy/Stow
#define Z_CLEARANCE_BETWEEN_PROBES  5 // Z Clearance between probe points
#define Z_CLEARANCE_MULTI_PROBE     5 // Z Clearance between multiple probes
#define Z_PROBE_LOW_POINT          -2 // Farthest distance below the trigger-point to go before stopping
#define Z_PROBE_OFFSET_RANGE_MIN -20
#define Z_PROBE_OFFSET_RANGE_MAX 20
#define X_ENABLE_ON 0
#define Y_ENABLE_ON 0
#define Z_ENABLE_ON 0
#define E_ENABLE_ON 0 // For all extruders
#define DISABLE_X false
#define DISABLE_Y false
#define DISABLE_Z false
#define DISABLE_E false // For all extruders
#define DISABLE_INACTIVE_EXTRUDER true // Keep only the active extruder enabled.
#define INVERT_X_DIR false
#define INVERT_Y_DIR false
#define INVERT_Z_DIR true
#define INVERT_E0_DIR true
#define INVERT_E1_DIR true
#define INVERT_E2_DIR false
#define INVERT_E3_DIR false
#define INVERT_E4_DIR false
#define X_HOME_DIR -1
#define Y_HOME_DIR -1
#define Z_HOME_DIR -1
#define X_BED_SIZE 340
#define Y_BED_SIZE 380
#define X_MIN_POS 0
#define Y_MIN_POS 0
#define Z_MIN_POS 0
#define X_MAX_POS X_BED_SIZE
#define Y_MAX_POS Y_BED_SIZE
#define Z_MAX_POS 330
#define MIN_SOFTWARE_ENDSTOPS
  #define MIN_SOFTWARE_ENDSTOP_X
  #define MIN_SOFTWARE_ENDSTOP_Y
#define MAX_SOFTWARE_ENDSTOPS
  #define MAX_SOFTWARE_ENDSTOP_X
  #define MAX_SOFTWARE_ENDSTOP_Y
  #define MAX_SOFTWARE_ENDSTOP_Z
#define FILAMENT_RUNOUT_SENSOR
  #define NUM_RUNOUT_SENSORS   1     // Number of sensors, up to one per extruder. Define a FIL_RUNOUT#_PIN for each.
  #define FIL_RUNOUT_INVERTING false // set to true to invert the logic of the sensor.
  #define FIL_RUNOUT_PULLUP          // Use internal pullup for filament runout pins.
  #define FILAMENT_RUNOUT_SCRIPT "M600"
#define AUTO_BED_LEVELING_3POINT
#define RESTORE_LEVELING_AFTER_G28
  #define PROBE_PT_1_X 30
  #define PROBE_PT_1_Y 30
  #define PROBE_PT_2_X 30
  #define PROBE_PT_2_Y 350
  #define PROBE_PT_3_X 330
  #define PROBE_PT_3_Y 190
#define LCD_BED_LEVELING
  #define MBL_Z_STEP 0.025    // Step size while manually probing Z axis.
  #define LCD_PROBE_Z_RANGE 4 // Z Range centered on Z_MIN_POS for LCD Z adjustment
#define LEVEL_BED_CORNERS
  #define LEVEL_CORNERS_INSET 30    // (mm) An inset for corner leveling
#define Z_SAFE_HOMING
  #define Z_SAFE_HOMING_X_POINT ((X_BED_SIZE) / 2)    // X point for Z homing when homing all axes (G28).
  #define Z_SAFE_HOMING_Y_POINT ((Y_BED_SIZE) / 2)    // Y point for Z homing when homing all axes (G28).
#define HOMING_FEEDRATE_XY (50*60)
#define HOMING_FEEDRATE_Z  (4*60)
#define EEPROM_SETTINGS // Enable for M500 and M501 commands
#define EEPROM_CHITCHAT   // Give feedback on EEPROM commands. Disable to save PROGMEM.
#define HOST_KEEPALIVE_FEATURE        // Disable this if your host doesn't like keepalive messages
#define DEFAULT_KEEPALIVE_INTERVAL 2  // Number of seconds between "busy" messages. Set with M113.
#define BUSY_WHILE_HEATING            // Some hosts require "busy" messages even during heating
#define PREHEAT_1_TEMP_HOTEND 180
#define PREHEAT_1_TEMP_BED     60
#define PREHEAT_1_FAN_SPEED     0 // Value from 0 to 255
#define PREHEAT_2_TEMP_HOTEND 240
#define PREHEAT_2_TEMP_BED    80
#define PREHEAT_2_FAN_SPEED     0 // Value from 0 to 255
#define NOZZLE_PARK_FEATURE
  #define NOZZLE_PARK_POINT { (X_MIN_POS + 10), (Y_MAX_POS - 10), 20 }
  #define NOZZLE_PARK_XY_FEEDRATE 100   // X and Y axes feedrate in mm/s (also used for delta printers Z axis)
  #define NOZZLE_PARK_Z_FEEDRATE 5      // Z axis feedrate in mm/s (not used for delta printers)
#define PRINTJOB_TIMER_AUTOSTART
#define PRINTCOUNTER
#define LCD_LANGUAGE en
#define DISPLAY_CHARSET_HD44780 JAPANESE
#define SDSUPPORT
#define REVERSE_ENCODER_DIRECTION
#define REPRAP_DISCOUNT_FULL_GRAPHIC_SMART_CONTROLLER
#define SOFT_PWM_SCALE 0
#define SERVO_DELAY { 300 }

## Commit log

2019-01-20 BOM update (partial)
    Partial BOM update for 500mm version
    [V-King CoreXY - Part Order List.xlsx]
2019-01-28 BOM updates
    Different BOM with supplier links to Aliexpress.
    [V-King CoreXY - Part Order List.xlsx]
2021-04-09 Create bullshit.step
    Added bullshit
    [bullshit.step]

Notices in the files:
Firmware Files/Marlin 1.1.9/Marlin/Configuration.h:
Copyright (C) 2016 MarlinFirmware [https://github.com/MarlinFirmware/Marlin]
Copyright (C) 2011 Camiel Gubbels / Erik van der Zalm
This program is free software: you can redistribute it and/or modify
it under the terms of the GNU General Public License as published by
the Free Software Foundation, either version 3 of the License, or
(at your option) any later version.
